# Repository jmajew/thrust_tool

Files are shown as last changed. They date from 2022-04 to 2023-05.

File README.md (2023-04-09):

# ThrustTool #

The ThrustTool is a DIY tool for measurements of an electric motor with propeller.
It allows to measure thrust, torque, rotation speed, battery voltage and current.

The project is by no means finished (especially firmware thrust++ and ThrustApp). However in current stage it works quite well allowing to obtain the results
(e.g., see auto generated report (in latex) [T-Motor F1507 with t3140 propeller](ThrustApp/data/tmotor-f1507/f1507_t3140_4s.pdf)).

### The project includes:

* [the 3d-printed tool](Doc/Tool.md)
* [custom board based on STM32 F401 mcu](Doc/Board.md)
* [firmware for the custom board](Doc/Firmware.md)
* [QT application for measurement managing and reporting](Doc/ThrustApp.md)

### 3D render of the tool
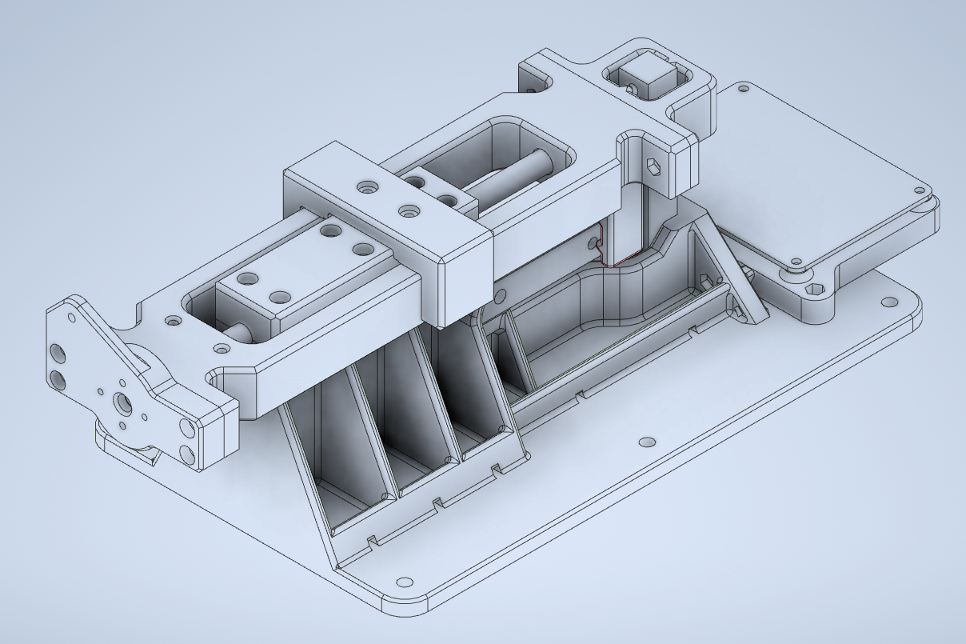
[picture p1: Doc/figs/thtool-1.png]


## Warning ##

The project is delivered as is. All responsibilities lies on the side of the user. 
Remember to take adequate security measures when testing any motor (especially powerful one).

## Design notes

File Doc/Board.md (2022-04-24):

## Custom board - thrustBoard v2

Custom measurement board (thrustBoard v2) is based on STM32 F401RETx LQFP64 MCU. 
The schematic of the thrustBoard v2 is [here](../Board/thrust_v2.pdf).

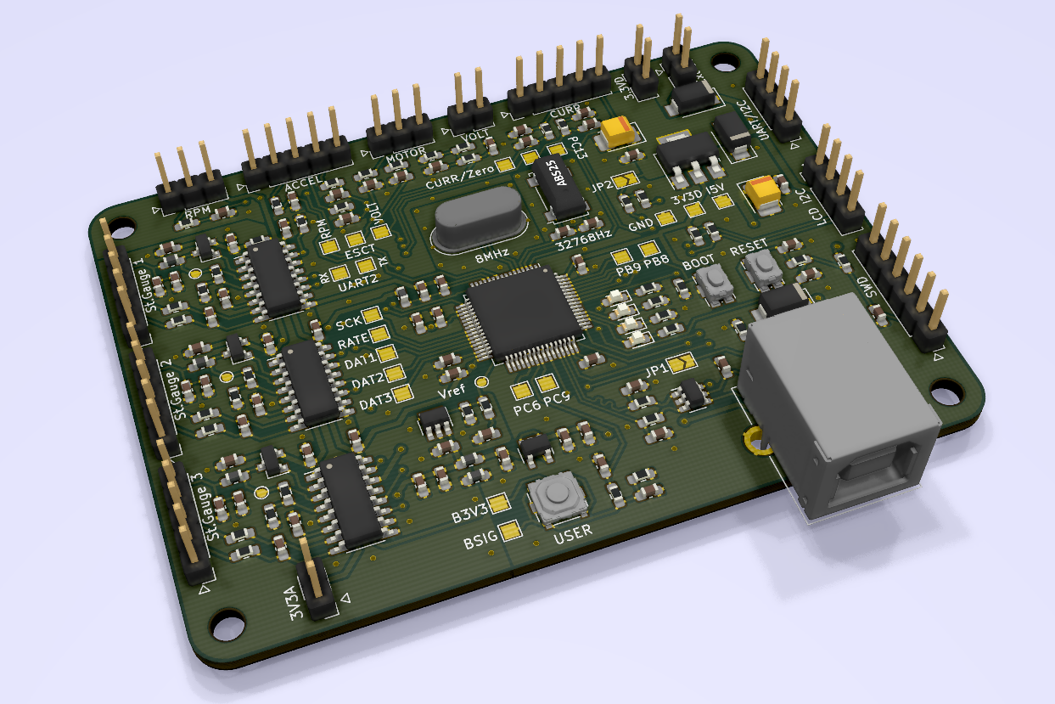
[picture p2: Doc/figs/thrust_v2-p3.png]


### Main features of the board:
* the physical board size is 84mm x 61mm.
* 3x channels of HX711 (24-Bit ADC for weight scales) - only 2 of them are actually used
* 8x 12-Bit ADC built-in inside the MCU used for battery voltage, current (2 channels), reference voltage, analog accelerometer (3 channels), MCU temperature
* SWD interface used for programming and debugging
* 1x UART or I2C communication for some future use
* 1x LCD with I2C interface to show some diagnostic data
* USB used communication with the board
* the board is powered by the USB but it is also possible use external 5V power source
* reset button, boot button (not used since programming is done by SWD), user button (currently not used in firmware)

### Recommended parts to use with the board:
* [Current sensors base on Hall sensor](https://www.pololu.com/category/118/current-sensors);
  some sensor require two channels of ADC one for current measurement and another for zero current
* ESC motor controller with telemetry (allows to obtain RPMs without additional infrared sensor), 
  e.g., [Tekko32 F3 Metal ESC (65A)](http://www.holybro.com/product/tekko32-f3-metal-esc-65a/)

### Additional notes:
- JP1 when closed allows to use USB_VBUS
- JP2 when closed enables pull-up resistor when UART/I2C is used as I2C 
- RTC crystal is not really currently needed. It was added for some possible future ideas.

### Front and back of the thrustBoard v2:
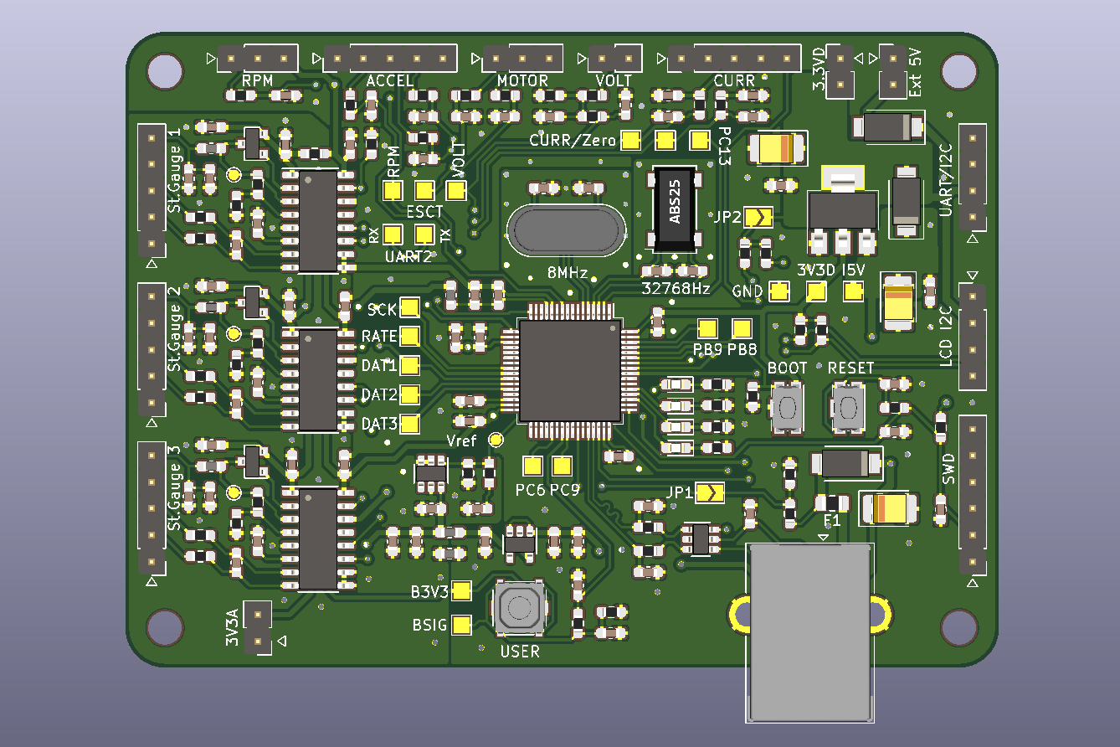
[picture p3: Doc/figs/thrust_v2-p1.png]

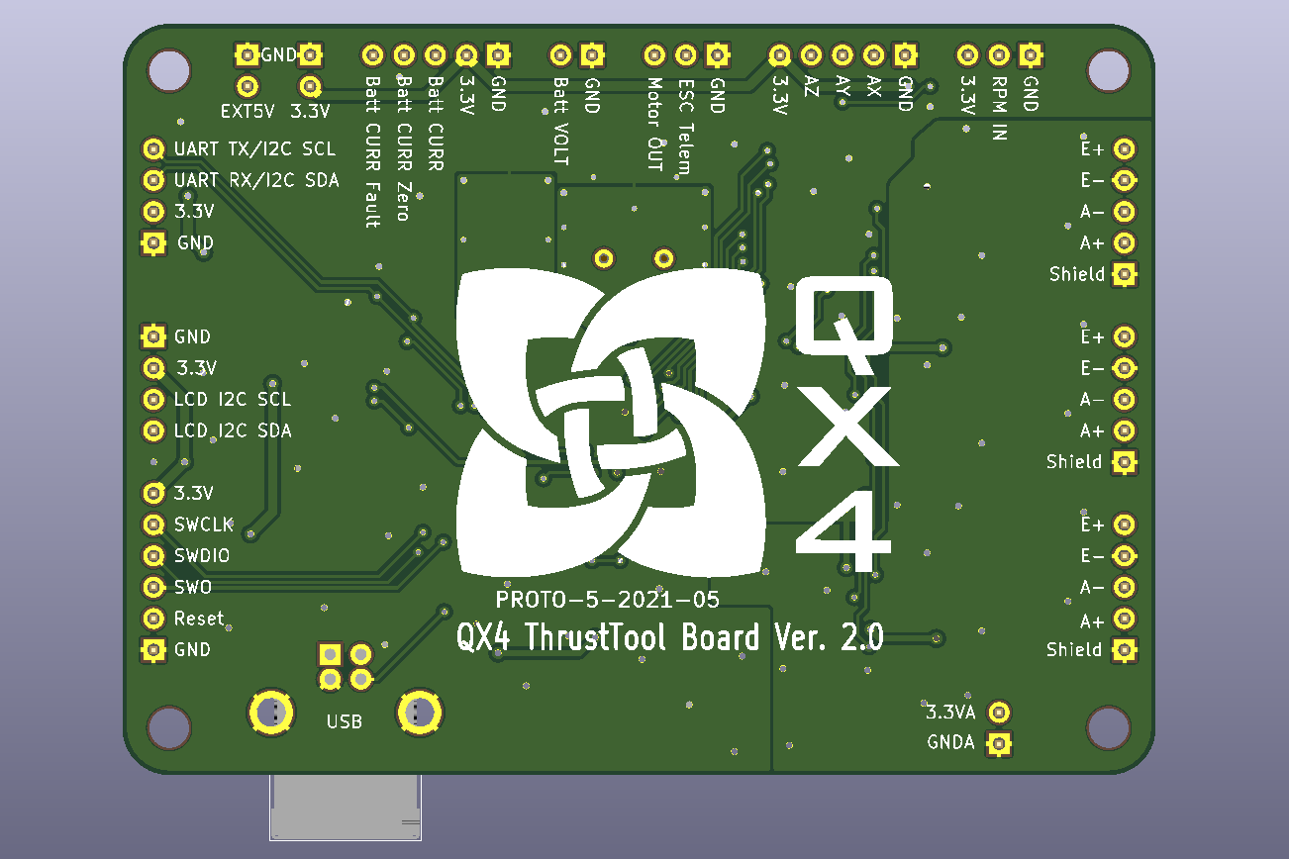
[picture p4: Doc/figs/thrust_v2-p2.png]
back


### Note

It is possible to use standard STM32 Nucleo F401RE board equipped with additional HX711 sensor boards instead of the thrustBoard v2.
Such approach require some experimenting both with hardware and firmware in order to map the pins, etc., properly.

### Picture of the board:
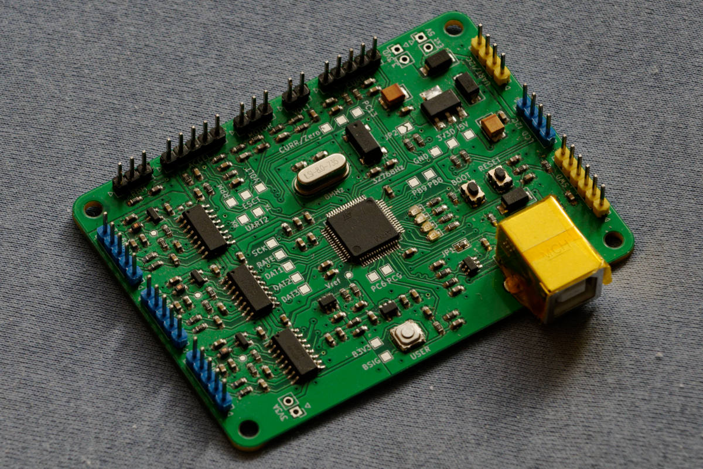
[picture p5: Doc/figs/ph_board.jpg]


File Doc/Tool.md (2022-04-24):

## Tool (3D printed)

The tool is built around two load cells: first for thrust and second for torque measurement. 
I have used load cells: 1kG for torque and 2kG for thrust - they allow measurements with resolution around 0.1G for thrust and 0.25 Gcm for torque.
The propeller should be mounted as a pusher such that flow stream behind propeller is not interacting with the tool and remain undisturbed.

### Half section of the tool:
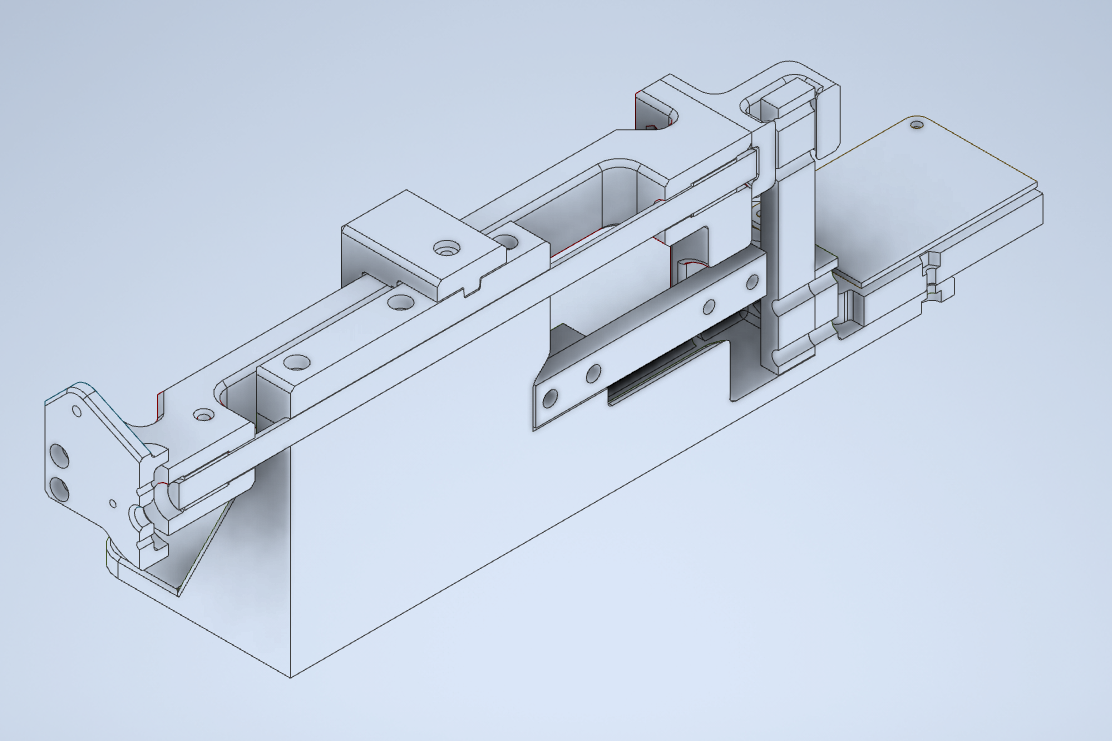
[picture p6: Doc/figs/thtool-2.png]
half section of the tool


### 3D-printed parts:
printed using PLA and without any support:
* stand
* axle mount
* spindle - use 4 perimeters
* thrust adapter
* lock - used to protect the load cells against excessive forces during, ex. transportation
* board mount
* motor mount - this part should be designed according to the motor specification, with or without infrared RPM sensor. 
  In case motor gets hot, more thermal resistant material should be used (PETG or even better ABS).

### Other elements:
* metal rod 8mm x 200mm
* [2 x plain bearing 8mm/10mm x 12mm](https://www.tme.eu/pl/en/details/wsm-0810-12/plain-bearings/igus/)
* M3 screws and nuts (length: 25mm, 16mm)

### extra 3D-printed parts:
they are not necessary but can be helpful during calibration process:
* thrust calib tray
* torque calib arm

### Picture of the working tool:
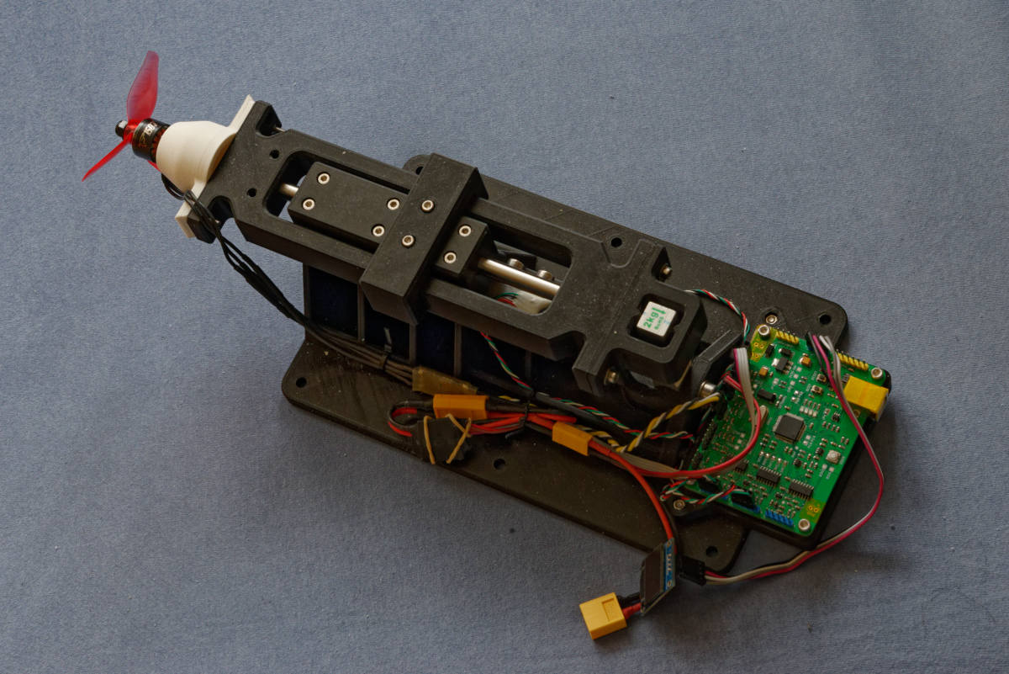
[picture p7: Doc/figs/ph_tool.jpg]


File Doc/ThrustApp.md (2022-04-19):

## ThrustApp 

ThrustApp is a QT application used for conducting measurement (tested in Win10 environment). 
It connects to the measurement board and by using serial protocol manages the process of data acquisition, receives the data
and present them in visual or tabular form. Finally it can processes the data and export a measurement report.

### Example view of the ThrustApp
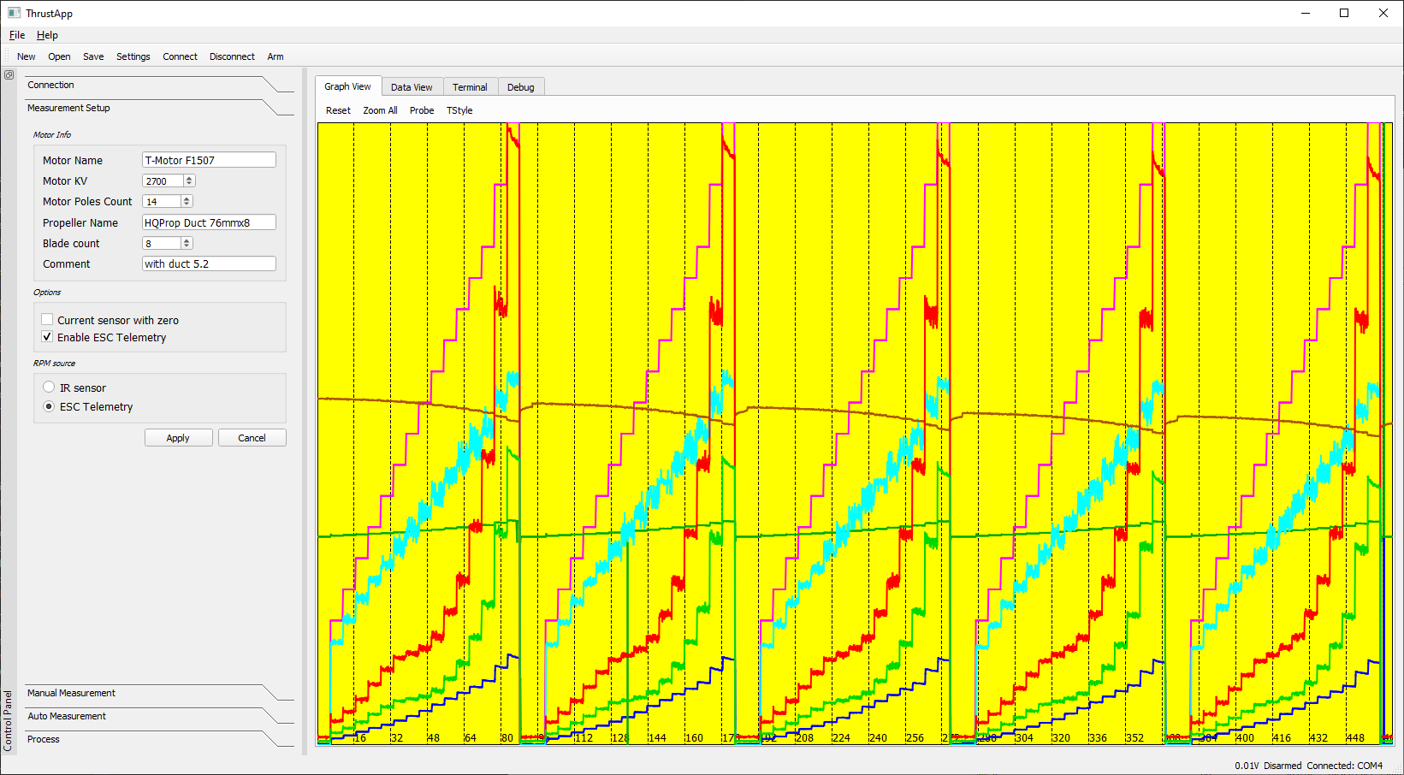
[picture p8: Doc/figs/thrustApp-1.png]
ThustApp


### Short description

The app is split in two areas: left is for controlling and right is for data presenting, terminal and protocol debugging.

#### Control widgets (for details see [Workflow](#workflow)):
* Connection
* Measurement Setup
* Manual Measurement - allows to manually start/stop data acquisition and start/stop motor with given output level (in micro-seconds)
* Auto Measurement
* Process

#### Main widgets:
* Graph View - shows data as a graph of multiple channels, both __raw__ and __cooked__. 
  It is possible to select what is shown by TStyle dialog (press *Color* to choose color, line style). 
  Ctrl+click can be used for zoom-window or Ctrl+wheel for zoom-in and zoom-out.
* Data View - shows data as a simple tabular array. Some column can be hidden for clarity
* Terminal - is used for low level connection to measurement board
* Debug - used for protocol debugging

### Workflow

* Connect to the tool via USB (the port should be visible as STMicroelectronics Virtual COM Port).
  Acceptable baud rate should be up to 500000. After successful connection info about board and firmware can be found in *Help/About* 
  and status bar should display *Connected: COMx*.
* In *Measurement Setup* put information about motor/propeller (needed only for reports) and select options. The tested options are 
  *ESC Telemetry* and *Enable ESC Telemetry*. Then press *Apply*.
* Select *Auto Measurement* and press button *Auto Create*. Choose starting and ending level and increment of motor output, 
  provide number of samples per single measurement (e.g., around 55-60 when using 10smpl/s) and 
  number of samples between measurements with motor output level 0% (preferably it should be 0). 
  After accepting the measurement table will be filled with values. You can still add or remove rows by mouse right-click menu.  
* Execute measurement setup by arming motor (main toolbar *Arm*) and pressing button *Measure Start*.
* Final step is processing data. The *Left margin* (e.g., around 10) and *Right margin* (e.g., around 4) 
  allows to select which part of single measurement is taken into account. This is necessary due to instabilities or delays with motor 
  response after changing the output level. The zero level is estimated taking into account all measurements with output level 0%.
* A report can be generated by choosing *File/Export* from menu. The report can exported as a text report
  (which contains only arrays of measurements) or as a latex file (can show also the plots). Before generating latex report, first
  the report template must be chosen (*File/Select Latex template*)

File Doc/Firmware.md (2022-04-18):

## Firmware thrust++

Firmware is written using C++ and [ChibiOS RTOS](https://www.chibios.org) (ver. ChibiOS RT 7.1.0 : HAL 8.1.0). 

The protocol implemented for communication with the window application is a derivative of the MSP protocol used if flight controller firmware 
(see, e.g., iNav or Betaflight). The terminal variables, reading and setting them is also derived from the flight controller firmware.

At the current stage of development the rpm measurements done using IR sensor needs some work. Therefore, the ESC telemetry should be  currently used as a source of the revolution speed measurement.

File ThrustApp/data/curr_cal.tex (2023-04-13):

\documentclass[10pt]{article}

\usepackage{pgfplots}
\usepackage{multirow}
\usepackage{filecontents}

\pgfplotsset{compat=1.14}

\usepackage[margin=20mm]{geometry}

\setlength{\textheight}{240 mm}

\begin{filecontents*}{table1.dat}
out,      th,    th_err, tq,     tq_err,  rpm,   rpm_err,  v,    v_err,   a,     a_err,   pin,        theff
    2e+01,       70.24,       0.323,      107.74,       2.373,        5496,        46.7,      14.736,      0.0057,       0.745,      0.0289,      10.977,       6.399
       40,      205.06,       0.344,      270.71,       2.376,        8753,        39.3,      14.471,      0.0069,       2.398,      0.0293,      34.701,       5.909
       45,      250.83,       0.585,      330.44,       2.421,        9594,        44.7,      14.340,      0.0075,       3.120,      0.0498,      44.743,       5.606
       50,      301.62,       0.747,      394.87,       2.535,       10477,        64.2,      14.193,      0.0091,       3.969,      0.0653,      56.334,       5.354
       55,      355.54,       0.714,      461.58,       2.437,       11337,        77.5,      14.018,      0.0101,       4.977,      0.0818,      69.771,       5.096
       60,      410.97,       0.735,      532.45,       2.432,       12162,        92.4,      13.821,      0.0118,       6.037,      0.0778,      83.441,       4.925
\end{filecontents*}

\begin{document}

\noindent
{\large \bf Tool info}
\vspace{3mm}

\noindent
\begin{tabular}{ll}
Serial API:  & \\ 
Board:       & \\ 
Firmware:    & \\ 
Commit:      & 
\end{tabular}
\vspace{3mm}

\noindent
{\large \bf Measurement info}
\vspace{3mm}

\noindent
\begin{tabular}{ll}
Motor:        & Generic Motor\\ 
KV:           & 0\\ 
Magnet poles: & 14\\ 
Propeler:     & \\ 
Blade count:  & 2\\ 
Note:         & 
\end{tabular}

\vspace{3mm}

%\noindent
%{\large \bf Measurement Results 1:}
%\vspace{3mm}

\subsection*{\large \bf Measurement Results 1:}

\noindent
\resizebox{\textwidth}{!}{
\begin{tabular}{|r|rr|rr|rr|rr|rr|r|r|}
\hline 
 \multirow[c]{2}{11mm}{Output [\%]} & \multicolumn{2}{l|}{Thrust [G]} & \multicolumn{2}{l|}{Torque [G cm]} & \multicolumn{2}{l|}{RPM [1/min]} 
   & \multicolumn{2}{l|}{Voltage [V]} & \multicolumn{2}{l|}{Current [A]} &\multirow{2}{14mm}{Pin [W]}  &\multirow{2}{14mm}{ThrustEff [G/W]}  \\
\cline{2-11} 
    &    mean& std dev&   mean& std dev&   mean& std dev&    mean& std dev&  mean& std dev&         &                \\
\hline
       20 &        70.24 &        0.323 &       107.74 &        2.373 &         5496 &         46.7 &       14.736 &       0.0057 &        0.745 &       0.0289 &       10.977 &        6.399 \\
       40 &       205.06 &        0.344 &       270.71 &        2.376 &         8753 &         39.3 &       14.471 &       0.0069 &        2.398 &       0.0293 &       34.701 &        5.909 \\
       45 &       250.83 &        0.585 &       330.44 &        2.421 &         9594 &         44.7 &       14.340 &       0.0075 &        3.120 &       0.0498 &       44.743 &        5.606 \\
       50 &       301.62 &        0.747 &       394.87 &        2.535 &        10477 &         64.2 &       14.193 &       0.0091 &        3.969 &       0.0653 &       56.334 &        5.354 \\
       55 &       355.54 &        0.714 &       461.58 &        2.437 &        11337 &         77.5 &       14.018 &       0.0101 &        4.977 &       0.0818 &       69.771 &        5.096 \\
       60 &       410.97 &        0.735 &       532.45 &        2.432 &        12162 &         92.4 &       13.821 &       0.0118 &        6.037 &       0.0778 &       83.441 &        4.925 \\
\hline
\end{tabular}
}

%\vspace{3mm}

\pagebreak
%\noindent
%{\large \bf Plots for Measurement Results:}
%\vspace{3mm}

\subsection*{Plots for Measurement Results:}
%\noindent
\centerline{
\hspace{-10mm}
\begin{tikzpicture}
	\begin{axis}[
		height=8cm,
		width=8cm,  %\textwidth,
		xmin=15,
		xmax=105,
		ymin=0,
		minor x tick num=3,
		minor y tick num=3,
		ticklabel style = {font=\tiny},
		grid=both,
		major grid style={gray!80},
		minor grid style={gray!25},
		xlabel={\footnotesize Motor Output [\%]},
		ylabel={\footnotesize Thrust [G]},
		%ylabel style={ yshift = {-1mm}, },
		legend pos=north west,
		legend style={draw=none}]
	\addplot[
		blue, mark options={black, scale=0.175},
		smooth, 
		error bars/.cd, 
		y fixed,
		y dir=both, 
		y explicit,
	] 
	table [x=out, y=th, y error=th_err, col sep=comma] {table1.dat};

	\end{axis}
\end{tikzpicture}
\hspace{5mm}
\begin{tikzpicture}
	\begin{axis}[
		height=8cm,
		width=8cm,  %\textwidth,
		xmin=15,
		xmax=105,
		ymin=0,
		minor x tick num=3,
		minor y tick num=3,
		ticklabel style = {font=\tiny},
		grid=both,
		major grid style={gray!80},
		minor grid style={gray!25},
		xlabel={\footnotesize Motor Output [\%]},
		ylabel={\footnotesize Torque [G cm]},
		legend pos=north west,
		legend style={draw=none}]
	\addplot[
		blue, mark options={black, scale=0.175},
		smooth, 
		error bars/.cd, 
		y fixed,
		y dir=both, 
		y explicit,
	] 
	table [x=out, y=tq, y error=tq_err, col sep=comma] {table1.dat};

	\end{axis}
\end{tikzpicture}
}
  
%\noindent 
\centerline{
\vspace{3mm}
\begin{tikzpicture}
	\begin{axis}[
		height=8cm,
		width=8cm,  %\textwidth,
		xmin=15,
		xmax=105,
		%ymin=0,
		minor x tick num=3,
		minor y tick num=3,	
		ticklabel style = {font=\tiny},
		tick scale binop=\times, %base 10:-3,
		grid=both,
		major grid style={gray!80},
		minor grid style={gray!25},
		xlabel={\footnotesize Motor Output [\%]},
		ylabel={\footnotesize RPM [1/min]},
		legend pos=north west,
		legend style={draw=none}]
	\addplot[
		blue, mark options={black, scale=0.175},
		smooth, 
		error bars/.cd, 
			y fixed,
			y dir=both, 
			y explicit,
	] 
	table [x=out, y=rpm, y error=rpm_err, col sep=comma] {table1.dat};

	\end{axis}
\end{tikzpicture}
\hspace{4.65mm}
\begin{tikzpicture}
	\begin{axis}[
		height=8cm,
		width=8cm,
		axis y line*=right,		
		xmin=15,
		xmax=105,
		ymin=0,
		minor x tick num=3,
		ticklabel style = {font=\tiny},
		grid=both,
		xlabel={\footnotesize Motor Output [\%]},
		ylabel={\footnotesize Current [A]},
		legend pos=north west,
		legend style={draw=none}]
	\addplot[
	  blue, mark options={black, scale=0.175},
	  smooth, 
	  error bars/.cd, 
		y fixed,
		y dir=both, 
		y explicit
	] 
	table [x=out, y=a, y error=a_err, col sep=comma] {table1.dat};

	\end{axis}
	\begin{axis}[
		height=8cm,
		width=8cm,  %\textwidth,
		axis y line*=left,
		axis x line=none,
		scaled y ticks=false,
		ticklabel style = {font=\tiny},
		grid style=dashed,
		grid=major,
		ylabel={\footnotesize Voltage [V]},
		legend style={
			nodes={scale=0.5, transform shape},
			cells={anchor=east},
			% legend pos=south east,
			at={(0.5,0.97)},anchor=north,
		}
	]
%	\addlegendimage{/pgfplots/refstyle=plot_1}\addlegendentry{Current [A]}
	\addplot[
		red, mark options={red, scale=0.15},
		smooth,
		error bars/.cd, 
		y fixed,
		y dir=both, 
		y explicit  
	] 
	table [x=out, y=v, y error=v_err, col sep=comma] {table1.dat};

%	\addlegendentry{Voltage [V]}
	\end{axis}
\end{tikzpicture}
\vspace{3mm}
}

%\noindent 
\centerline{
\hspace{-10mm}
\begin{tikzpicture}
	\begin{axis}[
		height=8cm,
		width=8cm,  %\textwidth,
		xmin=15,
		xmax=105,
		ymin=0,
		minor x tick num=3,
		minor y tick num=3,		
		ticklabel style = {font=\tiny},
		grid=both,
		major grid style={gray!80},
		minor grid style={gray!25},
		xlabel={\footnotesize Motor Output [\%]},
		ylabel={\footnotesize Power In [W]},
		legend pos=north west,
		legend style={
			nodes={scale=0.75, transform shape},
			cells={anchor=west},
			legend pos=north west,
		}	
	]			
	\addplot[
		blue, mark=*, mark options={blue, scale=0.5},
		smooth, 
	] 
	table [x=out, y=pin, col sep=comma] {table1.dat};

	\end{axis}
\end{tikzpicture}
\hspace{9mm}
\begin{tikzpicture}
	\begin{axis}[
		height=8cm,
		width=8cm,  %\textwidth,
		xmin=15,
		xmax=105,
		minor x tick num=3,
		minor y tick num=3,
		ticklabel style = {font=\tiny},
		grid=both,
		major grid style={gray!80},
		minor grid style={gray!25},
		xlabel={\footnotesize Motor Output [\%]},
		ylabel={\footnotesize Thrust Efficiency [G/W]},
		legend pos=north west,
		legend style={draw=none}]
	\addplot[
		blue, mark=*, mark options={blue, scale=0.5},
		smooth, 
	] 
	table [x=out, y=theff, col sep=comma] {table1.dat};

	\end{axis}
\end{tikzpicture}
}
	
\end{document}

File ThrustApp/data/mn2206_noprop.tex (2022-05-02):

\documentclass[10pt]{article}

\usepackage{pgfplots}
\usepackage{multirow}
\usepackage{filecontents}

\pgfplotsset{compat=1.14}

\usepackage[margin=20mm]{geometry}

\setlength{\textheight}{240 mm}

\begin{filecontents*}{table1.dat}
out,      th,    th_err, tq,     tq_err,  rpm,   rpm_err,  v,    v_err,   a,     a_err,   pin,        theff
    2e+01,        0.75,       4.004,        4.67,       3.013,        4759,        10.9,      12.141,      0.0039,       0.130,      0.0088,       1.580,       0.474
       25,        0.65,       4.004,        4.80,       3.013,        5899,        17.7,      12.140,      0.0041,       0.166,      0.0126,       2.014,       0.323
       30,       -0.30,       4.005,        4.98,       3.013,        7108,        27.4,      12.141,      0.0049,       0.188,      0.0129,       2.287,      -0.129
       35,       -0.30,       4.004,        5.04,       3.013,        8272,        32.6,      12.135,      0.0042,       0.242,      0.0171,       2.942,      -0.104
       40,       -0.38,       4.004,        5.62,       3.013,        9472,        56.0,      12.133,      0.0031,       0.263,      0.0177,       3.194,      -0.119
       45,       -1.53,       4.004,        4.44,       3.014,       10621,        81.1,      12.134,      0.0052,       0.294,      0.0325,       3.573,      -0.430
       50,       -2.90,       4.004,        4.27,       3.013,       11750,        85.6,      12.129,      0.0038,       0.322,      0.0218,       3.900,      -0.744
       55,       -3.37,       4.004,        3.33,       3.014,       12883,        89.5,      12.127,      0.0044,       0.373,      0.0309,       4.520,      -0.746
       60,       -3.35,       4.004,        2.68,       3.015,       14102,        69.3,      12.123,      0.0040,       0.403,      0.0262,       4.890,      -0.684
       65,       -3.38,       4.004,        1.43,       3.044,       15312,        95.8,      12.123,      0.0040,       0.429,      0.0445,       5.203,      -0.650
       70,       -3.38,       4.004,        0.38,       3.015,       16479,       119.5,      12.121,      0.0039,       0.455,      0.0333,       5.512,      -0.614
       75,       -3.38,       4.004,        0.92,       3.018,       17717,        80.4,      12.119,      0.0047,       0.470,      0.0248,       5.698,      -0.593
       80,       -7.57,       4.043,        5.10,       3.017,       18809,       122.2,      12.116,      0.0043,       0.488,      0.0333,       5.915,      -1.280
       90,       -4.35,       4.005,        6.84,       3.013,       21142,        92.4,      12.113,      0.0035,       0.535,      0.0127,       6.485,      -0.671
      100,       -0.64,       4.009,        4.66,       3.014,       23243,       100.8,      12.109,      0.0048,       0.592,      0.0144,       7.167,      -0.089
\end{filecontents*}

\begin{document}

\noindent
{\large \bf Tool info}
\vspace{3mm}

\noindent
\begin{tabular}{ll}
Serial API:  & 1:1.0\\ 
Board:       & Custom STM32F401RE thrustBoard v2\\ 
Firmware:    & thrust++ : ChibiOS RT 7.1.0 : HAL 8.1.0\\ 
Commit:      & [7ea798b] : Apr 25 2022 - 18:19:20
\end{tabular}
\vspace{3mm}

\noindent
{\large \bf Measurement info}
\vspace{3mm}

\noindent
\begin{tabular}{ll}
Motor:        & T-Motor MN2206-13\\ 
KV:           & 2000\\ 
Magnet poles: & 14\\ 
Propeler:     & no propeller\\ 
Blade count:  & 0\\ 
Note:         & 
\end{tabular}

\vspace{3mm}

\noindent
{\large \bf Measurement Results 1:}
\vspace{3mm}

\noindent
\resizebox{\textwidth}{!}{
\begin{tabular}{|r|rr|rr|rr|rr|rr|r|r|}
\hline 
 \multirow[c]{2}{11mm}{Output [\%]} & \multicolumn{2}{l|}{Thrust [G]} & \multicolumn{2}{l|}{Torque [G cm]} & \multicolumn{2}{l|}{RPM [1/min]} 
   & \multicolumn{2}{l|}{Voltage [V]} & \multicolumn{2}{l|}{Current [A]} &\multirow{2}{14mm}{Pin [W]}  &\multirow{2}{14mm}{ThrustEff [G/W]}  \\
\cline{2-11} 
    &    mean& std dev&   mean& std dev&   mean& std dev&    mean& std dev&  mean& std dev&         &                \\
\hline
       20 &         0.75 &        4.004 &         4.67 &        3.013 &         4759 &         10.9 &       12.141 &       0.0039 &        0.130 &       0.0088 &        1.580 &        0.474 \\
       25 &         0.65 &        4.004 &         4.80 &        3.013 &         5899 &         17.7 &       12.140 &       0.0041 &        0.166 &       0.0126 &        2.014 &        0.323 \\
       30 &        -0.30 &        4.005 &         4.98 &        3.013 &         7108 &         27.4 &       12.141 &       0.0049 &        0.188 &       0.0129 &        2.287 &       -0.129 \\
       35 &        -0.30 &        4.004 &         5.04 &        3.013 &         8272 &         32.6 &       12.135 &       0.0042 &        0.242 &       0.0171 &        2.942 &       -0.104 \\
       40 &        -0.38 &        4.004 &         5.62 &        3.013 &         9472 &         56.0 &       12.133 &       0.0031 &        0.263 &       0.0177 &        3.194 &       -0.119 \\
       45 &        -1.53 &        4.004 &         4.44 &        3.014 &        10621 &         81.1 &       12.134 &       0.0052 &        0.294 &       0.0325 &        3.573 &       -0.430 \\
       50 &        -2.90 &        4.004 &         4.27 &        3.013 &        11750 &         85.6 &       12.129 &       0.0038 &        0.322 &       0.0218 &        3.900 &       -0.744 \\
       55 &        -3.37 &        4.004 &         3.33 &        3.014 &        12883 &         89.5 &       12.127 &       0.0044 &        0.373 &       0.0309 &        4.520 &       -0.746 \\
       60 &        -3.35 &        4.004 &         2.68 &        3.015 &        14102 &         69.3 &       12.123 &       0.0040 &        0.403 &       0.0262 &        4.890 &       -0.684 \\
       65 &        -3.38 &        4.004 &         1.43 &        3.044 &        15312 &         95.8 &       12.123 &       0.0040 &        0.429 &       0.0445 &        5.203 &       -0.650 \\
       70 &        -3.38 &        4.004 &         0.38 &        3.015 &        16479 &        119.5 &       12.121 &       0.0039 &        0.455 &       0.0333 &        5.512 &       -0.614 \\
       75 &        -3.38 &        4.004 &         0.92 &        3.018 &        17717 &         80.4 &       12.119 &       0.0047 &        0.470 &       0.0248 &        5.698 &       -0.593 \\
       80 &        -7.57 &        4.043 &         5.10 &        3.017 &        18809 &        122.2 &       12.116 &       0.0043 &        0.488 &       0.0333 &        5.915 &       -1.280 \\
       90 &        -4.35 &        4.005 &         6.84 &        3.013 &        21142 &         92.4 &       12.113 &       0.0035 &        0.535 &       0.0127 &        6.485 &       -0.671 \\
      100 &        -0.64 &        4.009 &         4.66 &        3.014 &        23243 &        100.8 &       12.109 &       0.0048 &        0.592 &       0.0144 &        7.167 &       -0.089 \\
\hline
\end{tabular}
}

\vspace{3mm}

\pagebreak
\noindent
{\large \bf Plots for Measurement Results:}
\vspace{5mm}

\noindent
\begin{tikzpicture}
	\begin{axis}[
		height=8cm,
		width=8cm,  %\textwidth,
		ticklabel style = {font=\tiny},
		minor tick num=4,
		ymin=0,
		grid=both,
		major grid style={gray!80},
		minor grid style={gray!25},
		xlabel={\footnotesize Motor Output [\%]},
		ylabel={\footnotesize Thrust [G]},
		legend pos=north west,
		legend style={draw=none}]
	\addplot[
		blue, mark options={black, scale=0.175},
		smooth, 
		error bars/.cd, 
		y fixed,
		y dir=both, 
		y explicit,
	] 
	table [x=out, y=th, y error=th_err, col sep=comma] {table1.dat};

	\end{axis}
\end{tikzpicture}
\hspace{3mm}
\begin{tikzpicture}
	\begin{axis}[
		height=8cm,
		width=8cm,  %\textwidth,
		ticklabel style = {font=\tiny},
		minor tick num=4,
		ymin=0,
		grid=both,
		major grid style={gray!80},
		minor grid style={gray!25},
		xlabel={\footnotesize Motor Output [\%]},
		ylabel={\footnotesize Torque [G cm]},
		legend pos=north west,
		legend style={draw=none}]
	\addplot[
		blue, mark options={black, scale=0.175},
		smooth, 
		error bars/.cd, 
		y fixed,
		y dir=both, 
		y explicit,
	] 
	table [x=out, y=tq, y error=tq_err, col sep=comma] {table1.dat};

	\end{axis}
\end{tikzpicture}
  
\noindent 
\vspace{3mm}
\begin{tikzpicture}
	\begin{axis}[
		height=8cm,
		width=8cm,  %\textwidth,
		ticklabel style = {font=\tiny},
		tick scale binop=\times, %base 10:-3,
		minor tick num=4,
		grid=both,
		major grid style={gray!80},
		minor grid style={gray!25},
		xlabel={\footnotesize Motor Output [\%]},
		ylabel={\footnotesize RPM [1/min]},
		legend pos=north west,
		legend style={draw=none}]
	\addplot[
		blue, mark options={black, scale=0.175},
		smooth, 
		error bars/.cd, 
			y fixed,
			y dir=both, 
			y explicit,
	] 
	table [x=out, y=rpm, y error=rpm_err, col sep=comma] {table1.dat};

	\end{axis}
\end{tikzpicture}
\hspace{4.65mm}
\begin{tikzpicture}
	\begin{axis}[
		height=8cm,
		width=8cm,
		ticklabel style = {font=\tiny},
		ymin=0,
		grid=both,
		xlabel={\footnotesize Motor Output [\%]},
		ylabel={\footnotesize Current [A]},
		legend pos=north west,
		legend style={draw=none}]
	\addplot[
	  blue, mark options={black, scale=0.175},
	  smooth, 
	  error bars/.cd, 
		y fixed,
		y dir=both, 
		y explicit
	] 
	table [x=out, y=a, y error=a_err, col sep=comma] {table1.dat};

	\end{axis}
	\begin{axis}[
		height=8cm,
		width=8cm,  %\textwidth,
		axis y line*=right,
		axis x line=none,
		scaled y ticks=false,
		ticklabel style = {font=\tiny},
		grid style=dashed,
		grid=major,
		ylabel={\footnotesize Voltage [V]},
		legend style={
			nodes={scale=0.5, transform shape},
			cells={anchor=east},
			% legend pos=south east,
			at={(0.5,0.97)},anchor=north,
		}
	]
%	\addlegendimage{/pgfplots/refstyle=plot_1}\addlegendentry{Current [A]}
	\addplot[
		red, mark options={red, scale=0.15},
		smooth,
		error bars/.cd, 
		y fixed,
		y dir=both, 
		y explicit  
	] 
	table [x=out, y=v, y error=v_err, col sep=comma] {table1.dat};

%	\addlegendentry{Voltage [V]}
	\end{axis}
\end{tikzpicture}
\vspace{3mm}

\noindent 
\begin{tikzpicture}
	\begin{axis}[
		height=8cm,
		width=8cm,  %\textwidth,
		ticklabel style = {font=\tiny},
		minor tick num=4,
		ymin=0,
		grid=both,
		major grid style={gray!80},
		minor grid style={gray!25},
		xlabel={\footnotesize Motor Output [\%]},
		ylabel={\footnotesize Power In [W]},
		legend pos=north west,
		legend style={
			nodes={scale=0.75, transform shape},
			cells={anchor=west},
			legend pos=north west,
		}	
	]			
	\addplot[
		blue, mark=*, mark options={blue, scale=0.5},
		smooth, 
	] 
	table [x=out, y=pin, col sep=comma] {table1.dat};

	\end{axis}
	\end{tikzpicture}
\hspace{3mm}
	\begin{tikzpicture}
	\begin{axis}[
		height=8cm,
		width=8cm,  %\textwidth,
		ticklabel style = {font=\tiny},
		minor tick num=4,
		grid=both,
		major grid style={gray!80},
		minor grid style={gray!25},
		xlabel={\footnotesize Motor Output [\%]},
		ylabel={\footnotesize Thrust Efficiency [G/W]},
		legend pos=north west,
		legend style={draw=none}]
	\addplot[
		blue, mark=*, mark options={blue, scale=0.5},
		smooth, 
	] 
	table [x=out, y=theff, col sep=comma] {table1.dat};

	\end{axis}
\end{tikzpicture}

\end{document}

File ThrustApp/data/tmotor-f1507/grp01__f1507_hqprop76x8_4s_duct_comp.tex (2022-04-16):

\documentclass[10pt]{article}

\usepackage{pgfplots}
\usepackage{multirow}
\usepackage{filecontents}

\pgfplotsset{compat=1.14}

\usepackage[margin=20mm]{geometry}

\setlength{\textheight}{240 mm}

% \begin{filecontents*}{table1.dat}
% out,      th,    th_err, tq,     tq_err,  rpm,   rpm_err,  v,    v_err,   a,     a_err,   pin,        theff,
    % 2e+01,       28.52,       0.352,       48.79,       1.484,        7792,        69.8,      16.667,      0.0058,       0.479,      0.0181,       7.976,       3.575,
       % 25,       45.73,       0.413,       75.40,       1.658,        9613,       106.7,      16.651,      0.0086,       0.752,      0.0213,      12.515,       3.654,
       % 30,       67.16,       0.353,      107.87,       1.504,       11336,       114.7,      16.624,      0.0085,       1.097,      0.0282,      18.233,       3.683,
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
       60,      211.97,       1.136,      325.09,       1.014,       19533,       583.1,      16.358,      0.0109,       2.317,      0.0438,      37.908,       5.592
       65,      243.71,       0.752,      369.21,       1.334,       20708,       426.4,      16.284,      0.0133,       2.926,      0.0548,      47.641,       5.115
       70,      278.24,       0.840,      411.30,       1.363,       22175,       511.6,      16.196,      0.0127,       3.798,      0.0963,      61.514,       4.523
       75,      309.61,       2.277,      463.93,       3.978,       23169,       449.1,      16.097,      0.0126,       5.096,      0.0732,      82.030,       3.774
       80,      339.82,       3.009,      514.46,       4.794,       24354,       545.8,      15.990,      0.0097,       6.883,      0.0699,     110.062,       3.088
       90,      410.71,       2.651,      602.54,       5.925,       26446,       456.2,      15.806,      0.0173,      11.040,      0.1127,     174.498,       2.354
      100,      460.15,       3.974,      689.96,       7.139,       27885,       318.5,      15.596,      0.0183,      15.245,      0.1090,     237.763,       1.935
\end{filecontents*}

\begin{filecontents*}{table2.dat}
out,      th,    th_err, tq,     tq_err,  rpm,   rpm_err,  v,    v_err,   a,     a_err,   pin,        theff,
    2e+01,       36.19,       0.901,       43.11,       0.289,        8233,        87.6,      16.675,      0.0065,       0.391,      0.0140,       6.524,       5.547
       25,       54.59,       0.774,       68.57,       0.268,       10014,       116.3,      16.657,      0.0091,       0.622,      0.0186,      10.360,       5.269
       30,       78.09,       0.777,       91.36,       0.381,       11772,       157.1,      16.632,      0.0084,       0.932,      0.0206,      15.494,       5.040
       35,      101.89,       0.824,      121.68,       0.569,       13238,       188.5,      16.608,      0.0076,       1.298,      0.0205,      21.550,       4.728
       40,      121.84,       0.830,      145.77,       0.749,       14480,       169.5,      16.576,      0.0078,       1.651,      0.0263,      27.369,       4.452
       45,      148.23,       0.844,      174.95,       0.907,       15979,       523.5,      16.541,      0.0093,       1.943,      0.0254,      32.141,       4.612
       50,      177.38,       0.891,      214.64,       0.795,       17415,       300.2,      16.494,      0.0112,       2.052,      0.0259,      33.843,       5.241
       55,      209.49,       0.896,      254.91,       1.193,       18673,       435.7,      16.435,      0.0111,       2.183,      0.0356,      35.875,       5.839
       60,      248.30,       1.149,      287.80,       1.215,       20116,       556.9,      16.372,      0.0092,       2.478,      0.0411,      40.566,       6.121
       65,      286.57,       1.603,      338.44,       2.536,       21542,       518.3,      16.297,      0.0157,       3.087,      0.0412,      50.310,       5.696
       70,      323.12,       1.204,      380.84,       2.177,       22909,       526.4,      16.216,      0.0113,       3.863,      0.0609,      62.637,       5.159
       75,      360.33,       1.595,      432.03,       1.998,       24258,       720.2,      16.121,      0.0118,       5.183,      0.0600,      83.550,       4.313
       80,      398.91,       1.761,      471.44,       2.419,       25330,       403.9,      16.013,      0.0137,       6.872,      0.0843,     110.043,       3.625
       90,      485.15,       3.696,      571.83,       6.384,       27755,       416.2,      15.827,      0.0174,      10.574,      0.1176,     167.343,       2.899
      100,      551.97,       6.166,      651.32,      10.546,       29308,       283.0,      15.616,      0.0170,      14.701,      0.1102,     229.564,       2.404
\end{filecontents*}

\begin{document}

\noindent
{\large \bf Tool info}
\vspace{3mm}

\noindent
\begin{tabular}{ll}
Serial API : 	&1:1.0  \\
Board	:		&Custom STM32F401RE thrustBoard v2  \\
Firmware :		&thrust++ : ChibiOS RT 7.1.0 : HAL 8.1.0  \\
Commit :		&[28e06d2] : Mar 20 2022 - 17:31:34
\end{tabular}
\vspace{3mm}

\noindent
{\large \bf Measurement info}
\vspace{3mm}

\noindent
\begin{tabular}{ll}
Motor : 		&T-Motor F1507  \\
KV : 			&2700  \\
Magnet poles : 	&14  \\

Propeler : 		&HQProp Duct 76mmx8 \\
Blade number : 	&8  \\
Note :			&comparison of the performance with and without the duct
\end{tabular}

\vspace{3mm}

\noindent
{\large \bf Measurement Results without Duct:}
\vspace{3mm}

% \noindent
% \resizebox{\textwidth}{!}{
% \begin{tabular}{|r|rr|rr|rr|rr|rr|r|r|}
% \hline 
 % \multirow[c]{2}{11mm}{Output [\%]} & \multicolumn{2}{l|}{Thrust [G]} & \multicolumn{2}{l|}{Torque [G cm]} & \multicolumn{2}{l|}{RPM [1/min]} 
   % & \multicolumn{2}{l|}{Voltage [V]} & \multicolumn{2}{l|}{Current [A]} &\multirow{2}{14mm}{Pin [W]}  &\multirow{2}{14mm}{ThrustEff [G/W]}  \\
% \cline{2-11} 
    % &    mean& std dev&   mean& std dev&   mean& std dev&    mean& std dev&  mean& std dev&         &                \\
% \hline
       % 20 &        28.52 &        0.352 &        48.79 &        1.484 &         7792 &         69.8 &       16.667 &       0.0058 &        0.479 &       0.0181 &        7.976 &        3.575 \\
       % 25 &        45.73 &        0.413 &        75.40 &        1.658 &         9613 &        106.7 &       16.651 &       0.0086 &        0.752 &       0.0213 &       12.515 &        3.654 \\
       % 30 &        67.16 &        0.353 &       107.87 &        1.504 &        11336 &        114.7 &       16.624 &       0.0085 &        1.097 &       0.0282 &       18.233 &        3.683 \\
       % 35 &        89.74 &        0.622 &       145.08 &        1.508 &        13035 &        244.1 &       16.590 &       0.0072 &        1.349 &       0.0319 &       22.377 &        4.010 \\
       % 40 &       116.48 &        0.525 &       184.78 &        1.530 &        14636 &        359.5 &       16.545 &       0.0079 &        1.732 &       0.0391 &       28.650 &        4.066 \\
       % 45 &       140.28 &        0.459 &       223.05 &        1.544 &        16144 &        432.4 &       16.498 &       0.0092 &        2.276 &       0.0577 &       37.552 &        3.736 \\
       % 50 &       159.23 &        0.803 &       263.47 &        1.655 &        17443 &        254.6 &       16.440 &       0.0088 &        2.895 &       0.0497 &       47.590 &        3.346 \\
       % 55 &       199.86 &        0.717 &       306.46 &        1.758 &        18786 &        642.6 &       16.378 &       0.0086 &        3.828 &       0.0309 &       62.691 &        3.188 \\
       % 60 &       225.03 &        0.488 &       347.42 &        1.872 &        19902 &        409.7 &       16.314 &       0.0117 &        4.784 &       0.0448 &       78.042 &        2.883 \\
       % 65 &       261.16 &        1.146 &       389.64 &        2.552 &        20940 &        490.7 &       16.243 &       0.0103 &        5.820 &       0.0559 &       94.541 &        2.762 \\
       % 70 &       288.82 &        0.846 &       424.86 &        2.126 &        22056 &        467.9 &       16.159 &       0.0125 &        6.790 &       0.0551 &      109.720 &        2.632 \\
       % 75 &       315.84 &        1.026 &       473.27 &        2.894 &        23069 &        813.1 &       16.064 &       0.0099 &        7.525 &       0.0396 &      120.886 &        2.613 \\
       % 80 &       339.84 &        0.699 &       512.42 &        2.396 &        24065 &        974.1 &       15.968 &       0.0133 &        8.138 &       0.0612 &      129.947 &        2.615 \\
       % 85 &       370.79 &        2.068 &       544.51 &        4.284 &        25095 &        346.5 &       15.862 &       0.0127 &        9.382 &       0.1184 &      148.818 &        2.492 \\
       % 90 &       400.86 &        1.511 &       583.28 &        3.054 &        25929 &        513.5 &       15.755 &       0.0146 &       11.318 &       0.0954 &      178.317 &        2.248 \\
       % 95 &       424.20 &        2.412 &       622.93 &        5.510 &        26641 &        399.7 &       15.637 &       0.0140 &       13.168 &       0.0827 &      205.906 &        2.060 \\
      % 100 &       442.41 &        3.998 &       661.31 &        5.523 &        27154 &        224.3 &       15.523 &       0.0112 &       14.947 &       0.0646 &      232.017 &        1.907 \\
% \hline
% \end{tabular}
% }
\noindent
\resizebox{\textwidth}{!}{
\begin{tabular}{|r|rr|rr|rr|rr|rr|r|r|}
\hline 
 \multirow[c]{2}{11mm}{Output [\%]} & \multicolumn{2}{l|}{Thrust [G]} & \multicolumn{2}{l|}{Torque [G cm]} & \multicolumn{2}{l|}{RPM [1/min]} 
   & \multicolumn{2}{l|}{Voltage [V]} & \multicolumn{2}{l|}{Current [A]} &\multirow{2}{14mm}{Pin [W]}  &\multirow{2}{14mm}{ThrustEff [G/W]}  \\
\cline{2-11} 
    &    mean& std dev&   mean& std dev&   mean& std dev&    mean& std dev&  mean& std dev&         &                \\
\hline
       20 &        30.04 &        0.208 &        49.06 &        0.202 &         8138 &        121.4 &       16.668 &       0.0072 &        0.408 &       0.0121 &        6.800 &        4.417 \\
       25 &        47.24 &        0.273 &        73.99 &        0.350 &         9842 &         80.8 &       16.649 &       0.0073 &        0.664 &       0.0181 &       11.058 &        4.273 \\
       30 &        66.96 &        0.173 &       103.19 &        0.222 &        11444 &        115.9 &       16.627 &       0.0081 &        0.988 &       0.0145 &       16.424 &        4.077 \\
       35 &        85.92 &        0.248 &       131.30 &        0.202 &        12763 &        243.4 &       16.601 &       0.0075 &        1.346 &       0.0201 &       22.352 &        3.844 \\
       40 &       106.30 &        0.386 &       163.26 &        0.409 &        14104 &        252.7 &       16.567 &       0.0074 &        1.766 &       0.0253 &       29.257 &        3.633 \\
       45 &       125.50 &        0.404 &       195.91 &        0.415 &        15512 &        376.6 &       16.529 &       0.0099 &        1.924 &       0.0267 &       31.798 &        3.947 \\
       50 &       144.74 &        2.850 &       234.91 &        1.405 &        16786 &        404.6 &       16.480 &       0.0082 &        1.971 &       0.0373 &       32.486 &        4.456 \\
       55 &       181.63 &        0.499 &       275.72 &        0.804 &        18267 &        291.4 &       16.427 &       0.0127 &        2.083 &       0.0535 &       34.224 &        5.307 \\
       60 &       211.97 &        1.136 &       325.09 &        1.014 &        19533 &        583.1 &       16.358 &       0.0109 &        2.317 &       0.0438 &       37.908 &        5.592 \\
       65 &       243.71 &        0.752 &       369.21 &        1.334 &        20708 &        426.4 &       16.284 &       0.0133 &        2.926 &       0.0548 &       47.641 &        5.115 \\
       70 &       278.24 &        0.840 &       411.30 &        1.363 &        22175 &        511.6 &       16.196 &       0.0127 &        3.798 &       0.0963 &       61.514 &        4.523 \\
       75 &       309.61 &        2.277 &       463.93 &        3.978 &        23169 &        449.1 &       16.097 &       0.0126 &        5.096 &       0.0732 &       82.030 &        3.774 \\
       80 &       339.82 &        3.009 &       514.46 &        4.794 &        24354 &        545.8 &       15.990 &       0.0097 &        6.883 &       0.0699 &      110.062 &        3.088 \\
       90 &       410.71 &        2.651 &       602.54 &        5.925 &        26446 &        456.2 &       15.806 &       0.0173 &       11.040 &       0.1127 &      174.498 &        2.354 \\
      100 &       460.15 &        3.974 &       689.96 &        7.139 &        27885 &        318.5 &       15.596 &       0.0183 &       15.245 &       0.1090 &      237.763 &        1.935 \\
\hline
\end{tabular}
}

\vspace{3mm}

\noindent
{\large \bf Measurement Results with Duct:}
\vspace{3mm}

\noindent
\resizebox{\textwidth}{!}{
\begin{tabular}{|r|rr|rr|rr|rr|rr|r|r|}
\hline 
 \multirow[c]{2}{11mm}{Output [\%]} & \multicolumn{2}{l|}{Thrust [G]} & \multicolumn{2}{l|}{Torque [G cm]} & \multicolumn{2}{l|}{RPM [1/min]} 
   & \multicolumn{2}{l|}{Voltage [V]} & \multicolumn{2}{l|}{Current [A]} &\multirow{2}{14mm}{Pin [W]}  &\multirow{2}{14mm}{ThrustEff [G/W]}  \\
\cline{2-11} 
    &    mean& std dev&   mean& std dev&   mean& std dev&    mean& std dev&  mean& std dev&         &                \\
\hline
       20 &        36.19 &        0.901 &        43.11 &        0.289 &         8233 &         87.6 &       16.675 &       0.0065 &        0.391 &       0.0140 &        6.524 &        5.547 \\
       25 &        54.59 &        0.774 &        68.57 &        0.268 &        10014 &        116.3 &       16.657 &       0.0091 &        0.622 &       0.0186 &       10.360 &        5.269 \\
       30 &        78.09 &        0.777 &        91.36 &        0.381 &        11772 &        157.1 &       16.632 &       0.0084 &        0.932 &       0.0206 &       15.494 &        5.040 \\
       35 &       101.89 &        0.824 &       121.68 &        0.569 &        13238 &        188.5 &       16.608 &       0.0076 &        1.298 &       0.0205 &       21.550 &        4.728 \\
       40 &       121.84 &        0.830 &       145.77 &        0.749 &        14480 &        169.5 &       16.576 &       0.0078 &        1.651 &       0.0263 &       27.369 &        4.452 \\
       45 &       148.23 &        0.844 &       174.95 &        0.907 &        15979 &        523.5 &       16.541 &       0.0093 &        1.943 &       0.0254 &       32.141 &        4.612 \\
       50 &       177.38 &        0.891 &       214.64 &        0.795 &        17415 &        300.2 &       16.494 &       0.0112 &        2.052 &       0.0259 &       33.843 &        5.241 \\
       55 &       209.49 &        0.896 &       254.91 &        1.193 &        18673 &        435.7 &       16.435 &       0.0111 &        2.183 &       0.0356 &       35.875 &        5.839 \\
       60 &       248.30 &        1.149 &       287.80 &        1.215 &        20116 &        556.9 &       16.372 &       0.0092 &        2.478 &       0.0411 &       40.566 &        6.121 \\
       65 &       286.57 &        1.603 &       338.44 &        2.536 &        21542 &        518.3 &       16.297 &       0.0157 &        3.087 &       0.0412 &       50.310 &        5.696 \\
       70 &       323.12 &        1.204 &       380.84 &        2.177 &        22909 &        526.4 &       16.216 &       0.0113 &        3.863 &       0.0609 &       62.637 &        5.159 \\
       75 &       360.33 &        1.595 &       432.03 &        1.998 &        24258 &        720.2 &       16.121 &       0.0118 &        5.183 &       0.0600 &       83.550 &        4.313 \\
       80 &       398.91 &        1.761 &       471.44 &        2.419 &        25330 &        403.9 &       16.013 &       0.0137 &        6.872 &       0.0843 &      110.043 &        3.625 \\
       90 &       485.15 &        3.696 &       571.83 &        6.384 &        27755 &        416.2 &       15.827 &       0.0174 &       10.574 &       0.1176 &      167.343 &        2.899 \\
      100 &       551.97 &        6.166 &       651.32 &       10.546 &        29308 &        283.0 &       15.616 &       0.0170 &       14.701 &       0.1102 &      229.564 &        2.404 \\
\hline
\end{tabular}
}

\vspace{3mm}

%%%%%%%%%%%%%%%%%%%%%%%%%%%%%%%%%%%%%%%%%%%%%%%%%%%%%%%%%%%%%%%%%%%%%%%%%%%%%%%%%%%%%%%%%%%%

\pagebreak
\noindent
{\large \bf Plots for Measurement Results:}
\vspace{5mm}

\noindent
\begin{tikzpicture}
	\begin{axis}[
		height=8cm,
		width=8cm,  %\textwidth,
		ticklabel style = {font=\tiny},
		minor tick num=4,
		ymin=0,
		grid=both,
		major grid style={gray!80},
		minor grid style={gray!25},
		xlabel={\footnotesize Motor Output [\%]},
		ylabel={\footnotesize Thrust [G]},
		legend pos=north west,
		legend style={draw=none}]
	\addplot[
		blue, mark options={black, scale=0.175},
		smooth, 
		error bars/.cd, 
		y fixed,
		y dir=both, 
		y explicit,
	] 
	table [x=out, y=th, y error=th_err, col sep=comma] {table1.dat};
	\addplot[
		red, mark options={black, scale=0.175},
		smooth, 
		error bars/.cd, 
		y fixed,
		y dir=both, 
		y explicit,
	] 
	table [x=out, y=th, y error=th_err, col sep=comma] {table2.dat};
	\end{axis}
\end{tikzpicture}
\hspace{3mm}
\begin{tikzpicture}
	\begin{axis}[
		height=8cm,
		width=8cm,  %\textwidth,
		ticklabel style = {font=\tiny},
		minor tick num=4,
		ymin=0,
		grid=both,
		major grid style={gray!80},
		minor grid style={gray!25},
		xlabel={\footnotesize Motor Output [\%]},
		ylabel={\footnotesize Torque [G cm]},
		legend pos=north west,
		legend style={draw=none}]
	\addplot[
		blue, mark options={black, scale=0.175},
		smooth, 
		error bars/.cd, 
		y fixed,
		y dir=both, 
		y explicit,
	] 
	table [x=out, y=tq, y error=tq_err, col sep=comma] {table1.dat};
	\addplot[
		red, mark options={black, scale=0.175},
		smooth, 
		error bars/.cd, 
		y fixed,
		y dir=both, 
		y explicit,
	] 
	table [x=out, y=tq, y error=tq_err, col sep=comma] {table2.dat};
	\end{axis}
\end{tikzpicture}
  
\noindent 
\vspace{2mm}
\begin{tikzpicture}
	\begin{axis}[
		height=8cm,
		width=8cm,  %\textwidth,
		ticklabel style = {font=\tiny},
		tick scale binop=\times, %base 10:-3,
		minor tick num=4,
		grid=both,
		major grid style={gray!80},
		minor grid style={gray!25},
		xlabel={\footnotesize Motor Output [\%]},
		ylabel={\footnotesize RPM [1/min]},
		legend pos=north west,
		legend style={draw=none}]
	\addplot[
		blue, mark options={black, scale=0.175},
		smooth, 
		error bars/.cd, 
			y fixed,
			y dir=both, 
			y explicit,
	] 
	table [x=out, y=rpm, y error=rpm_err, col sep=comma] {table1.dat};
	\addplot[
		red, mark options={black, scale=0.175},
		smooth, 
		error bars/.cd, 
			y fixed,
			y dir=both, 
			y explicit,
	] 
	table [x=out, y=rpm, y error=rpm_err, col sep=comma] {table2.dat};
	\end{axis}
\end{tikzpicture}
\hspace{4.65mm}
\begin{tikzpicture}
	\begin{axis}[
		height=8cm,
		width=8cm,
		ticklabel style = {font=\tiny},
		ymin=0,
		grid=both,
		xlabel={\footnotesize Motor Output [\%]},
		ylabel={\footnotesize Current [A]},
		legend pos=north west,
		legend style={draw=none}]
	\addplot[
	  blue, mark options={black, scale=0.175},
	  smooth, 
	  error bars/.cd, 
		y fixed,
		y dir=both, 
		y explicit
	] 
	table [x=out, y=a, y error=a_err, col sep=comma] {table1.dat}; \label{plot_1}
	\addplot[
	  red, mark options={black, scale=0.175},
	  smooth, 
	  error bars/.cd, 
		y fixed,
		y dir=both, 
		y explicit
	] 
	table [x=out, y=a, y error=a_err, col sep=comma] {table2.dat};
	\end{axis}
	\begin{axis}[
		height=8cm,
		width=8cm,  %\textwidth,
		axis y line*=right,
		axis x line=none,
		scaled y ticks=false,
		ticklabel style = {font=\tiny},
		grid style=dashed,
		grid=major,
		ylabel={\footnotesize Voltage [V]},
		legend style={
			nodes={scale=0.5, transform shape},
			cells={anchor=east},
			% legend pos=south east,
			at={(0.5,0.97)},anchor=north,
		}
	]
	% \addlegendimage{/pgfplots/refstyle=plot_1}\addlegendentry{Current [A]}
	\addplot[
		blue, mark options={red, scale=0.15},
		smooth,
		error bars/.cd, 
		y fixed,
		y dir=both, 
		y explicit  
	] 
	table [x=out, y=v, y error=v_err, col sep=comma] {table1.dat}; \label{plot_2}
	\addplot[
		red, mark options={red, scale=0.15},
		smooth,
		error bars/.cd, 
		y fixed,
		y dir=both, 
		y explicit  
	] 
	table [x=out, y=v, y error=v_err, col sep=comma] {table2.dat};
	% \addlegendentry{Voltage [V]}
	\end{axis}
\end{tikzpicture}
\vspace{2mm}

\noindent 
\begin{tikzpicture}
	\begin{axis}[
		height=8cm,
		width=8cm,  %\textwidth,
		ticklabel style = {font=\tiny},
		minor tick num=4,
		ymin=0,
		grid=both,
		major grid style={gray!80},
		minor grid style={gray!25},
		xlabel={\footnotesize Motor Output [\%]},
		ylabel={\footnotesize Power In [W]},
		legend pos=north west,
		legend style={
			nodes={scale=0.75, transform shape},
			cells={anchor=west},
			legend pos=north west,
		}	
	]			
	\addplot[
		blue, mark=*, mark options={blue, scale=0.5},
		smooth, 
	] 
	table [x=out, y=pin, col sep=comma] {table1.dat};
	\addplot[
		red, mark=*, mark options={red, scale=0.5},
		smooth, 
	] 
	table [x=out, y=pin, col sep=comma] {table2.dat};
	\end{axis}
	\end{tikzpicture}
\hspace{3mm}
	\begin{tikzpicture}
	\begin{axis}[
		height=8cm,
		width=8cm,  %\textwidth,
		ticklabel style = {font=\tiny},
		minor tick num=4,
		grid=both,
		major grid style={gray!80},
		minor grid style={gray!25},
		xlabel={\footnotesize Motor Output [\%]},
		ylabel={\footnotesize Thrust Efficiency [G/W]},
		legend pos=north west,
		legend style={draw=none}]
	\addplot[
		blue, mark=*, mark options={blue, scale=0.5},
		smooth, 
	] 
	table [x=out, y=theff, col sep=comma] {table1.dat};
	\addplot[
		red, mark=*, mark options={red, scale=0.5},
		smooth, 
	] 
	table [x=out, y=theff, col sep=comma] {table2.dat};
	\end{axis}
\end{tikzpicture}

%%%%%%%%%%%%%%%%%%%%%%%%%%%%%%%%%%%%%%%%%%%%%%%%%%%%%%%%%%%%%%%%%%%%%%%%%%%%%%%%%%%%%%%%%%%%

\end{document}

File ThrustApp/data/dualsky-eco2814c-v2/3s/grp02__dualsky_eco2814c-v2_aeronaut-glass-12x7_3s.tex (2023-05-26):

\documentclass[10pt]{article}

\usepackage{pgfplots}
\usepackage{multirow}
\usepackage{filecontents}

\pgfplotsset{compat=1.14}

\usepackage[margin=20mm]{geometry}

\setlength{\textheight}{240 mm}

\begin{filecontents*}{table1.dat}
out,      th,    th_err, tq,     tq_err,  rpm,   rpm_err,  v,    v_err,   a,     a_err,   pin,        theff
    2e+01,       59.05,       3.388,      155.61,      41.443,        1951,        45.0,      12.580,      0.0034,       0.665,      0.0292,       8.359,       7.065
       30,      169.89,       1.392,      334.89,      41.362,        2741,        13.2,      12.560,      0.0054,       1.406,      0.0317,      17.662,       9.619
       40,      329.78,       0.798,      632.93,      41.278,        3665,        22.3,      12.522,      0.0050,       2.998,      0.0317,      37.542,       8.784
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
       80,     1308.33,       4.292,     2367.85,      33.411,        6804,        68.1,      11.735,      0.0134,      19.135,      0.0781,     224.542,       5.827
       90,     1563.46,       4.962,     2853.03,      34.529,        7389,        60.4,      11.547,      0.0136,      25.436,      0.0934,     293.711,       5.323
      100,     1789.86,       4.983,     3285.37,      34.326,        7885,        44.8,      11.348,      0.0121,      32.216,      0.1413,     365.592,       4.896
\end{filecontents*}

\begin{filecontents*}{table4.dat}
out,      th,    th_err, tq,     tq_err,  rpm,   rpm_err,  v,    v_err,   a,     a_err,   pin,        theff
       20,       55.60,       3.723,      124.86,      70.330,        1880,        52.2,      11.983,      0.0045,       0.649,      0.0291,       7.775,       7.151
       30,      150.62,       0.936,      286.10,      70.241,        2618,        13.3,      11.968,      0.0038,       1.316,      0.0300,      15.750,       9.563
       40,      295.99,       0.877,      553.48,      70.244,        3500,        22.5,      11.933,      0.0037,       2.766,      0.0393,      33.011,       8.966
       50,      456.01,       1.188,      857.92,      70.246,        4260,        24.3,      11.879,      0.0044,       4.919,      0.0403,      58.426,       7.805
       60,      690.56,       2.310,     1267.16,      70.244,        5066,        40.0,      11.806,      0.0071,       8.291,      0.0435,      97.886,       7.055
       70,      978.17,       5.095,     1779.95,      70.270,        5958,        60.5,      11.686,      0.0072,      13.045,      0.0668,     152.450,       6.416
       80,     1273.62,       5.078,     2293.07,      70.335,        6737,        68.7,      11.548,      0.0091,      18.650,      0.0624,     215.370,       5.914
       90,     1541.85,       3.081,     2782.87,      70.395,        7347,        51.3,      11.393,      0.0094,      24.976,      0.0582,     284.565,       5.418
      100,     1761.74,       6.687,     3228.44,      71.004,        7853,        47.7,      11.218,      0.0090,      31.725,      0.2144,     355.878,       4.950
\end{filecontents*}

\begin{filecontents*}{table5.dat}
out,      th,    th_err, tq,     tq_err,  rpm,   rpm_err,  v,    v_err,   a,     a_err,   pin,        theff
       20,       54.76,       3.614,      115.21,      79.412,        1866,        50.6,      11.879,      0.0042,       0.630,      0.0286,       7.489,       7.313
       30,      147.73,       1.019,      273.10,      79.328,        2596,        12.5,      11.861,      0.0042,       1.304,      0.0221,      15.468,       9.550
       40,      289.28,       1.049,      534.78,      79.335,        3466,        18.3,      11.831,      0.0055,       2.701,      0.0312,      31.955,       9.053
       50,      449.03,       1.155,      834.73,      79.330,        4229,        24.2,      11.778,      0.0055,       4.852,      0.0390,      57.150,       7.857
       60,      677.71,       1.683,     1244.86,      79.335,        5044,        38.0,      11.695,      0.0089,       8.206,      0.0417,      95.971,       7.062
       70,      967.69,       2.307,     1742.69,      79.395,        5899,        64.9,      11.579,      0.0091,      12.885,      0.0691,     149.202,       6.486
       80,     1248.35,       7.365,     2246.33,      79.904,        6686,        66.2,      11.437,      0.0089,      18.387,      0.0918,     210.296,       5.936
       90,     1515.69,       5.962,     2737.18,      79.732,        7297,        51.0,      11.286,      0.0086,      24.603,      0.0857,     277.664,       5.459
      100,     1741.96,      11.526,     3179.97,      81.782,        7796,        47.4,      11.115,      0.0095,      31.307,      0.1693,     347.984,       5.006
\end{filecontents*}

\begin{document}

\noindent
{\large \bf Tool info}
\vspace{3mm}

\noindent
\begin{tabular}{ll}
Serial API:  & \\ 
Board:       & \\ 
Firmware:    & \\ 
Commit:      & 
\end{tabular}
\vspace{3mm}

\noindent
{\large \bf Measurement info}
\vspace{3mm}

\noindent
\begin{tabular}{ll}
Motor:        & Dualsky ECO2814C V2\\ 
KV:           & 970\\ 
Magnet poles: & 14\\ 
Propeler:     & Aerinaut Glass 12x7 fold\\ 
Blade count:  & 2\\ 
Note:         & Battery 3S 2600 mAh
\end{tabular}

\vspace{3mm}

%\noindent
%{\large \bf Measurement Results 1:}
%\vspace{3mm}

\subsection*{\large \bf Measurement Results 1:}

\noindent
\resizebox{\textwidth}{!}{
\begin{tabular}{|r|rr|rr|rr|rr|rr|r|r|}
\hline 
 \multirow[c]{2}{11mm}{Output [\%]} & \multicolumn{2}{l|}{Thrust [G]} & \multicolumn{2}{l|}{Torque [G cm]} & \multicolumn{2}{l|}{RPM [1/min]} 
   & \multicolumn{2}{l|}{Voltage [V]} & \multicolumn{2}{l|}{Current [A]} &\multirow{2}{14mm}{Pin [W]}  &\multirow{2}{14mm}{ThrustEff [G/W]}  \\
\cline{2-11} 
    &    mean& std dev&   mean& std dev&   mean& std dev&    mean& std dev&  mean& std dev&         &                \\
\hline
       20 &        59.05 &        3.388 &       155.61 &       41.443 &         1951 &         45.0 &       12.580 &       0.0034 &        0.665 &       0.0292 &        8.359 &        7.065 \\
       30 &       169.89 &        1.392 &       334.89 &       41.362 &         2741 &         13.2 &       12.560 &       0.0054 &        1.406 &       0.0317 &       17.662 &        9.619 \\
       40 &       329.78 &        0.798 &       632.93 &       41.278 &         3665 &         22.3 &       12.522 &       0.0050 &        2.998 &       0.0317 &       37.542 &        8.784 \\
       50 &       503.23 &        1.335 &       969.98 &       41.295 &         4459 &         24.6 &       12.466 &       0.0063 &        5.342 &       0.0553 &       66.598 &        7.556 \\
       60 &       740.36 &        1.963 &      1383.37 &       41.275 &         5231 &         42.2 &       12.381 &       0.0097 &        8.845 &       0.0486 &      109.513 &        6.760 \\
       70 &      1043.00 &        4.112 &      1947.29 &       41.409 &         6168 &         55.7 &       12.244 &       0.0091 &       13.888 &       0.0726 &      170.042 &        6.134 \\
       80 &      1381.31 &        4.494 &      2509.25 &       41.947 &         6988 &         63.2 &       12.078 &       0.0116 &       20.042 &       0.1080 &      242.070 &        5.706 \\
       90 &      1644.47 &        7.710 &      3017.16 &       43.223 &         7578 &         53.5 &       11.889 &       0.0111 &       26.714 &       0.1466 &      317.589 &        5.178 \\
      100 &      1902.23 &        7.706 &      3480.86 &       44.440 &         8084 &         46.7 &       11.685 &       0.0137 &       33.812 &       0.2027 &      395.105 &        4.814 \\
\hline
\end{tabular}
}

%\vspace{3mm}

%\noindent
%{\large \bf Measurement Results 2:}
%\vspace{3mm}

\subsection*{\large \bf Measurement Results 2:}

\noindent
\resizebox{\textwidth}{!}{
\begin{tabular}{|r|rr|rr|rr|rr|rr|r|r|}
\hline 
 \multirow[c]{2}{11mm}{Output [\%]} & \multicolumn{2}{l|}{Thrust [G]} & \multicolumn{2}{l|}{Torque [G cm]} & \multicolumn{2}{l|}{RPM [1/min]} 
   & \multicolumn{2}{l|}{Voltage [V]} & \multicolumn{2}{l|}{Current [A]} &\multirow{2}{14mm}{Pin [W]}  &\multirow{2}{14mm}{ThrustEff [G/W]}  \\
\cline{2-11} 
    &    mean& std dev&   mean& std dev&   mean& std dev&    mean& std dev&  mean& std dev&         &                \\
\hline
       20 &        54.79 &       13.899 &       150.24 &       38.980 &         1926 &         48.9 &       12.375 &       0.0039 &        0.660 &       0.0311 &        8.164 &        6.711 \\
       30 &       162.40 &        0.839 &       318.27 &       37.251 &         2705 &         14.7 &       12.359 &       0.0039 &        1.373 &       0.0312 &       16.970 &        9.570 \\
       40 &       319.25 &        0.891 &       610.65 &       37.257 &         3615 &         15.8 &       12.323 &       0.0058 &        2.943 &       0.0410 &       36.264 &        8.804 \\
       50 &       492.71 &        1.299 &       932.71 &       37.261 &         4382 &         21.9 &       12.268 &       0.0065 &        5.198 &       0.0414 &       63.767 &        7.727 \\
       60 &       723.29 &        3.301 &      1351.60 &       37.266 &         5195 &         45.4 &       12.175 &       0.0074 &        8.694 &       0.0473 &      105.851 &        6.833 \\
       70 &      1020.61 &        2.762 &      1884.38 &       37.383 &         6096 &         52.8 &       12.057 &       0.0089 &       13.604 &       0.0865 &      164.019 &        6.223 \\
       80 &      1335.44 &        4.103 &      2429.37 &       37.931 &         6874 &         65.3 &       11.908 &       0.0086 &       19.517 &       0.1022 &      232.405 &        5.746 \\
       90 &      1599.63 &        6.297 &      2920.87 &       38.675 &         7494 &         50.7 &       11.733 &       0.0100 &       25.976 &       0.1157 &      304.771 &        5.249 \\
      100 &      1843.81 &        9.411 &      3379.98 &       39.985 &         7981 &         49.9 &       11.545 &       0.0129 &       33.083 &       0.2150 &      381.936 &        4.828 \\
\hline
\end{tabular}
}

%\vspace{3mm}

%\noindent
%{\large \bf Measurement Results 3:}
%\vspace{3mm}

\subsection*{\large \bf Measurement Results 3:}

\noindent
\resizebox{\textwidth}{!}{
\begin{tabular}{|r|rr|rr|rr|rr|rr|r|r|}
\hline 
 \multirow[c]{2}{11mm}{Output [\%]} & \multicolumn{2}{l|}{Thrust [G]} & \multicolumn{2}{l|}{Torque [G cm]} & \multicolumn{2}{l|}{RPM [1/min]} 
   & \multicolumn{2}{l|}{Voltage [V]} & \multicolumn{2}{l|}{Current [A]} &\multirow{2}{14mm}{Pin [W]}  &\multirow{2}{14mm}{ThrustEff [G/W]}  \\
\cline{2-11} 
    &    mean& std dev&   mean& std dev&   mean& std dev&    mean& std dev&  mean& std dev&         &                \\
\hline
       20 &        57.58 &        4.216 &       142.03 &       33.204 &         1909 &         51.7 &       12.221 &       0.0035 &        0.653 &       0.0297 &        7.978 &        7.218 \\
       30 &       158.29 &        0.895 &       310.25 &       33.060 &         2667 &         14.5 &       12.206 &       0.0055 &        1.353 &       0.0386 &       16.518 &        9.583 \\
       40 &       311.32 &        0.984 &       591.73 &       33.077 &         3576 &         16.3 &       12.171 &       0.0057 &        2.878 &       0.0312 &       35.031 &        8.887 \\
       50 &       476.12 &        1.265 &       904.61 &       33.083 &         4333 &         23.8 &       12.119 &       0.0051 &        5.085 &       0.0309 &       61.621 &        7.727 \\
       60 &       708.62 &        2.072 &      1314.61 &       33.071 &         5142 &         47.4 &       12.031 &       0.0094 &        8.507 &       0.0521 &      102.350 &        6.924 \\
       70 &       996.75 &        4.141 &      1840.62 &       33.120 &         6031 &         38.7 &       11.903 &       0.0111 &       13.352 &       0.0871 &      158.922 &        6.272 \\
       80 &      1308.33 &        4.292 &      2367.85 &       33.411 &         6804 &         68.1 &       11.735 &       0.0134 &       19.135 &       0.0781 &      224.542 &        5.827 \\
       90 &      1563.46 &        4.962 &      2853.03 &       34.529 &         7389 &         60.4 &       11.547 &       0.0136 &       25.436 &       0.0934 &      293.711 &        5.323 \\
      100 &      1789.86 &        4.983 &      3285.37 &       34.326 &         7885 &         44.8 &       11.348 &       0.0121 &       32.216 &       0.1413 &      365.592 &        4.896 \\
\hline
\end{tabular}
}

%\vspace{3mm}

%\noindent
%{\large \bf Measurement Results 4:}
%\vspace{3mm}

\subsection*{\large \bf Measurement Results 4:}

\noindent
\resizebox{\textwidth}{!}{
\begin{tabular}{|r|rr|rr|rr|rr|rr|r|r|}
\hline 
 \multirow[c]{2}{11mm}{Output [\%]} & \multicolumn{2}{l|}{Thrust [G]} & \multicolumn{2}{l|}{Torque [G cm]} & \multicolumn{2}{l|}{RPM [1/min]} 
   & \multicolumn{2}{l|}{Voltage [V]} & \multicolumn{2}{l|}{Current [A]} &\multirow{2}{14mm}{Pin [W]}  &\multirow{2}{14mm}{ThrustEff [G/W]}  \\
\cline{2-11} 
    &    mean& std dev&   mean& std dev&   mean& std dev&    mean& std dev&  mean& std dev&         &                \\
\hline
       20 &        55.60 &        3.723 &       124.86 &       70.330 &         1880 &         52.2 &       11.983 &       0.0045 &        0.649 &       0.0291 &        7.775 &        7.151 \\
       30 &       150.62 &        0.936 &       286.10 &       70.241 &         2618 &         13.3 &       11.968 &       0.0038 &        1.316 &       0.0300 &       15.750 &        9.563 \\
       40 &       295.99 &        0.877 &       553.48 &       70.244 &         3500 &         22.5 &       11.933 &       0.0037 &        2.766 &       0.0393 &       33.011 &        8.966 \\
       50 &       456.01 &        1.188 &       857.92 &       70.246 &         4260 &         24.3 &       11.879 &       0.0044 &        4.919 &       0.0403 &       58.426 &        7.805 \\
       60 &       690.56 &        2.310 &      1267.16 &       70.244 &         5066 &         40.0 &       11.806 &       0.0071 &        8.291 &       0.0435 &       97.886 &        7.055 \\
       70 &       978.17 &        5.095 &      1779.95 &       70.270 &         5958 &         60.5 &       11.686 &       0.0072 &       13.045 &       0.0668 &      152.450 &        6.416 \\
       80 &      1273.62 &        5.078 &      2293.07 &       70.335 &         6737 &         68.7 &       11.548 &       0.0091 &       18.650 &       0.0624 &      215.370 &        5.914 \\
       90 &      1541.85 &        3.081 &      2782.87 &       70.395 &         7347 &         51.3 &       11.393 &       0.0094 &       24.976 &       0.0582 &      284.565 &        5.418 \\
      100 &      1761.74 &        6.687 &      3228.44 &       71.004 &         7853 &         47.7 &       11.218 &       0.0090 &       31.725 &       0.2144 &      355.878 &        4.950 \\
\hline
\end{tabular}
}

%\vspace{3mm}

%\noindent
%{\large \bf Measurement Results 5:}
%\vspace{3mm}

\subsection*{\large \bf Measurement Results 5:}

\noindent
\resizebox{\textwidth}{!}{
\begin{tabular}{|r|rr|rr|rr|rr|rr|r|r|}
\hline 
 \multirow[c]{2}{11mm}{Output [\%]} & \multicolumn{2}{l|}{Thrust [G]} & \multicolumn{2}{l|}{Torque [G cm]} & \multicolumn{2}{l|}{RPM [1/min]} 
   & \multicolumn{2}{l|}{Voltage [V]} & \multicolumn{2}{l|}{Current [A]} &\multirow{2}{14mm}{Pin [W]}  &\multirow{2}{14mm}{ThrustEff [G/W]}  \\
\cline{2-11} 
    &    mean& std dev&   mean& std dev&   mean& std dev&    mean& std dev&  mean& std dev&         &                \\
\hline
       20 &        54.76 &        3.614 &       115.21 &       79.412 &         1866 &         50.6 &       11.879 &       0.0042 &        0.630 &       0.0286 &        7.489 &        7.313 \\
       30 &       147.73 &        1.019 &       273.10 &       79.328 &         2596 &         12.5 &       11.861 &       0.0042 &        1.304 &       0.0221 &       15.468 &        9.550 \\
       40 &       289.28 &        1.049 &       534.78 &       79.335 &         3466 &         18.3 &       11.831 &       0.0055 &        2.701 &       0.0312 &       31.955 &        9.053 \\
       50 &       449.03 &        1.155 &       834.73 &       79.330 &         4229 &         24.2 &       11.778 &       0.0055 &        4.852 &       0.0390 &       57.150 &        7.857 \\
       60 &       677.71 &        1.683 &      1244.86 &       79.335 &         5044 &         38.0 &       11.695 &       0.0089 &        8.206 &       0.0417 &       95.971 &        7.062 \\
       70 &       967.69 &        2.307 &      1742.69 &       79.395 &         5899 &         64.9 &       11.579 &       0.0091 &       12.885 &       0.0691 &      149.202 &        6.486 \\
       80 &      1248.35 &        7.365 &      2246.33 &       79.904 &         6686 &         66.2 &       11.437 &       0.0089 &       18.387 &       0.0918 &      210.296 &        5.936 \\
       90 &      1515.69 &        5.962 &      2737.18 &       79.732 &         7297 &         51.0 &       11.286 &       0.0086 &       24.603 &       0.0857 &      277.664 &        5.459 \\
      100 &      1741.96 &       11.526 &      3179.97 &       81.782 &         7796 &         47.4 &       11.115 &       0.0095 &       31.307 &       0.1693 &      347.984 &        5.006 \\
\hline
\end{tabular}
}

%\vspace{3mm}

\pagebreak
%\noindent
%{\large \bf Plots for Measurement Results:}
%\vspace{3mm}

\subsection*{Plots for Measurement Results:}
%\noindent
\centerline{
\hspace{-10mm}
\begin{tikzpicture}
	\begin{axis}[
		height=8cm,
		width=8cm,  %\textwidth,
		xmin=15,
		xmax=105,
		ymin=0,
		minor x tick num=3,
		minor y tick num=3,
		ticklabel style = {font=\tiny},
		grid=both,
		major grid style={gray!80},
		minor grid style={gray!25},
		xlabel={\footnotesize Motor Output [\%]},
		ylabel={\footnotesize Thrust [G]},
		%ylabel style={ yshift = {-1mm}, },
		legend pos=north west,
		legend style={draw=none}]
	\addplot[
		blue, mark options={black, scale=0.175},
		smooth, 
		error bars/.cd, 
		y fixed,
		y dir=both, 
		y explicit,
	] 
	table [x=out, y=th, y error=th_err, col sep=comma] {table1.dat};
	\addplot[
		blue, mark options={black, scale=0.175},
		smooth, 
		error bars/.cd, 
		y fixed,
		y dir=both, 
		y explicit,
	] 
	table [x=out, y=th, y error=th_err, col sep=comma] {table2.dat};
	\addplot[
		blue, mark options={black, scale=0.175},
		smooth, 
		error bars/.cd, 
		y fixed,
		y dir=both, 
		y explicit,
	] 
	table [x=out, y=th, y error=th_err, col sep=comma] {table3.dat};
	\addplot[
		blue, mark options={black, scale=0.175},
		smooth, 
		error bars/.cd, 
		y fixed,
		y dir=both, 
		y explicit,
	] 
	table [x=out, y=th, y error=th_err, col sep=comma] {table4.dat};
	\addplot[
		blue, mark options={black, scale=0.175},
		smooth, 
		error bars/.cd, 
		y fixed,
		y dir=both, 
		y explicit,
	] 
	table [x=out, y=th, y error=th_err, col sep=comma] {table5.dat};

	\end{axis}
\end{tikzpicture}
\hspace{5mm}
\begin{tikzpicture}
	\begin{axis}[
		height=8cm,
		width=8cm,  %\textwidth,
		xmin=15,
		xmax=105,
		ymin=0,
		minor x tick num=3,
		minor y tick num=3,
		ticklabel style = {font=\tiny},
		grid=both,
		major grid style={gray!80},
		minor grid style={gray!25},
		xlabel={\footnotesize Motor Output [\%]},
		ylabel={\footnotesize Torque [G cm]},
		legend pos=north west,
		legend style={draw=none}]
	\addplot[
		blue, mark options={black, scale=0.175},
		smooth, 
		error bars/.cd, 
		y fixed,
		y dir=both, 
		y explicit,
	] 
	table [x=out, y=tq, y error=tq_err, col sep=comma] {table1.dat};
	\addplot[
		blue, mark options={black, scale=0.175},
		smooth, 
		error bars/.cd, 
		y fixed,
		y dir=both, 
		y explicit,
	] 
	table [x=out, y=tq, y error=tq_err, col sep=comma] {table2.dat};
	\addplot[
		blue, mark options={black, scale=0.175},
		smooth, 
		error bars/.cd, 
		y fixed,
		y dir=both, 
		y explicit,
	] 
	table [x=out, y=tq, y error=tq_err, col sep=comma] {table3.dat};
	\addplot[
		blue, mark options={black, scale=0.175},
		smooth, 
		error bars/.cd, 
		y fixed,
		y dir=both, 
		y explicit,
	] 
	table [x=out, y=tq, y error=tq_err, col sep=comma] {table4.dat};
	\addplot[
		blue, mark options={black, scale=0.175},
		smooth, 
		error bars/.cd, 
		y fixed,
		y dir=both, 
		y explicit,
	] 
	table [x=out, y=tq, y error=tq_err, col sep=comma] {table5.dat};

	\end{axis}
\end{tikzpicture}
}
  
%\noindent 
\centerline{
\vspace{3mm}
\begin{tikzpicture}
	\begin{axis}[
		height=8cm,
		width=8cm,  %\textwidth,
		xmin=15,
		xmax=105,
		%ymin=0,
		minor x tick num=3,
		minor y tick num=3,	
		ticklabel style = {font=\tiny},
		tick scale binop=\times, %base 10:-3,
		grid=both,
		major grid style={gray!80},
		minor grid style={gray!25},
		xlabel={\footnotesize Motor Output [\%]},
		ylabel={\footnotesize RPM [1/min]},
		legend pos=north west,
		legend style={draw=none}]
	\addplot[
		blue, mark options={black, scale=0.175},
		smooth, 
		error bars/.cd, 
			y fixed,
			y dir=both, 
			y explicit,
	] 
	table [x=out, y=rpm, y error=rpm_err, col sep=comma] {table1.dat};
	\addplot[
		blue, mark options={black, scale=0.175},
		smooth, 
		error bars/.cd, 
			y fixed,
			y dir=both, 
			y explicit,
	] 
	table [x=out, y=rpm, y error=rpm_err, col sep=comma] {table2.dat};
	\addplot[
		blue, mark options={black, scale=0.175},
		smooth, 
		error bars/.cd, 
			y fixed,
			y dir=both, 
			y explicit,
	] 
	table [x=out, y=rpm, y error=rpm_err, col sep=comma] {table3.dat};
	\addplot[
		blue, mark options={black, scale=0.175},
		smooth, 
		error bars/.cd, 
			y fixed,
			y dir=both, 
			y explicit,
	] 
	table [x=out, y=rpm, y error=rpm_err, col sep=comma] {table4.dat};
	\addplot[
		blue, mark options={black, scale=0.175},
		smooth, 
		error bars/.cd, 
			y fixed,
			y dir=both, 
			y explicit,
	] 
	table [x=out, y=rpm, y error=rpm_err, col sep=comma] {table5.dat};

	\end{axis}
\end{tikzpicture}
\hspace{4.65mm}
\begin{tikzpicture}
	\begin{axis}[
		height=8cm,
		width=8cm,
		axis y line*=right,		
		xmin=15,
		xmax=105,
		ymin=0,
		minor x tick num=3,
		ticklabel style = {font=\tiny},
		grid=both,
		xlabel={\footnotesize Motor Output [\%]},
		ylabel={\footnotesize Current [A]},
		legend pos=north west,
		legend style={draw=none}]
	\addplot[
	  blue, mark options={black, scale=0.175},
	  smooth, 
	  error bars/.cd, 
		y fixed,
		y dir=both, 
		y explicit
	] 
	table [x=out, y=a, y error=a_err, col sep=comma] {table1.dat};
	\addplot[
	  blue, mark options={black, scale=0.175},
	  smooth, 
	  error bars/.cd, 
		y fixed,
		y dir=both, 
		y explicit
	] 
	table [x=out, y=a, y error=a_err, col sep=comma] {table2.dat};
	\addplot[
	  blue, mark options={black, scale=0.175},
	  smooth, 
	  error bars/.cd, 
		y fixed,
		y dir=both, 
		y explicit
	] 
	table [x=out, y=a, y error=a_err, col sep=comma] {table3.dat};
	\addplot[
	  blue, mark options={black, scale=0.175},
	  smooth, 
	  error bars/.cd, 
		y fixed,
		y dir=both, 
		y explicit
	] 
	table [x=out, y=a, y error=a_err, col sep=comma] {table4.dat};
	\addplot[
	  blue, mark options={black, scale=0.175},
	  smooth, 
	  error bars/.cd, 
		y fixed,
		y dir=both, 
		y explicit
	] 
	table [x=out, y=a, y error=a_err, col sep=comma] {table5.dat};

	\end{axis}
	\begin{axis}[
		height=8cm,
		width=8cm,  %\textwidth,
		axis y line*=left,
		axis x line=none,
		scaled y ticks=false,
		ticklabel style = {font=\tiny},
		grid style=dashed,
		grid=major,
		ylabel={\footnotesize Voltage [V]},
		legend style={
			nodes={scale=0.5, transform shape},
			cells={anchor=east},
			% legend pos=south east,
			at={(0.5,0.97)},anchor=north,
		}
	]
%	\addlegendimage{/pgfplots/refstyle=plot_1}\addlegendentry{Current [A]}
	\addplot[
		red, mark options={red, scale=0.15},
		smooth,
		error bars/.cd, 
		y fixed,
		y dir=both, 
		y explicit  
	] 
	table [x=out, y=v, y error=v_err, col sep=comma] {table1.dat};
	\addplot[
		red, mark options={red, scale=0.15},
		smooth,
		error bars/.cd, 
		y fixed,
		y dir=both, 
		y explicit  
	] 
	table [x=out, y=v, y error=v_err, col sep=comma] {table2.dat};
	\addplot[
		red, mark options={red, scale=0.15},
		smooth,
		error bars/.cd, 
		y fixed,
		y dir=both, 
		y explicit  
	] 
	table [x=out, y=v, y error=v_err, col sep=comma] {table3.dat};
	\addplot[
		red, mark options={red, scale=0.15},
		smooth,
		error bars/.cd, 
		y fixed,
		y dir=both, 
		y explicit  
	] 
	table [x=out, y=v, y error=v_err, col sep=comma] {table4.dat};
	\addplot[
		red, mark options={red, scale=0.15},
		smooth,
		error bars/.cd, 
		y fixed,
		y dir=both, 
		y explicit  
	] 
	table [x=out, y=v, y error=v_err, col sep=comma] {table5.dat};

%	\addlegendentry{Voltage [V]}
	\end{axis}
\end{tikzpicture}
\vspace{3mm}
}

%\noindent 
\centerline{
\hspace{-10mm}
\begin{tikzpicture}
	\begin{axis}[
		height=8cm,
		width=8cm,  %\textwidth,
		xmin=15,
		xmax=105,
		ymin=0,
		minor x tick num=3,
		minor y tick num=3,		
		ticklabel style = {font=\tiny},
		grid=both,
		major grid style={gray!80},
		minor grid style={gray!25},
		xlabel={\footnotesize Motor Output [\%]},
		ylabel={\footnotesize Power In [W]},
		legend pos=north west,
		legend style={
			nodes={scale=0.75, transform shape},
			cells={anchor=west},
			legend pos=north west,
		}	
	]			
	\addplot[
		blue, mark=*, mark options={blue, scale=0.5},
		smooth, 
	] 
	table [x=out, y=pin, col sep=comma] {table1.dat};
	\addplot[
		blue, mark=*, mark options={blue, scale=0.5},
		smooth, 
	] 
	table [x=out, y=pin, col sep=comma] {table2.dat};
	\addplot[
		blue, mark=*, mark options={blue, scale=0.5},
		smooth, 
	] 
	table [x=out, y=pin, col sep=comma] {table3.dat};
	\addplot[
		blue, mark=*, mark options={blue, scale=0.5},
		smooth, 
	] 
	table [x=out, y=pin, col sep=comma] {table4.dat};
	\addplot[
		blue, mark=*, mark options={blue, scale=0.5},
		smooth, 
	] 
	table [x=out, y=pin, col sep=comma] {table5.dat};

	\end{axis}
\end{tikzpicture}
\hspace{9mm}
\begin{tikzpicture}
	\begin{axis}[
		height=8cm,
		width=8cm,  %\textwidth,
		xmin=15,
		xmax=105,
		minor x tick num=3,
		minor y tick num=3,
		ticklabel style = {font=\tiny},
		grid=both,
		major grid style={gray!80},
		minor grid style={gray!25},
		xlabel={\footnotesize Motor Output [\%]},
		ylabel={\footnotesize Thrust Efficiency [G/W]},
		legend pos=north west,
		legend style={draw=none}]
	\addplot[
		blue, mark=*, mark options={blue, scale=0.5},
		smooth, 
	] 
	table [x=out, y=theff, col sep=comma] {table1.dat};
	\addplot[
		blue, mark=*, mark options={blue, scale=0.5},
		smooth, 
	] 
	table [x=out, y=theff, col sep=comma] {table2.dat};
	\addplot[
		blue, mark=*, mark options={blue, scale=0.5},
		smooth, 
	] 
	table [x=out, y=theff, col sep=comma] {table3.dat};
	\addplot[
		blue, mark=*, mark options={blue, scale=0.5},
		smooth, 
	] 
	table [x=out, y=theff, col sep=comma] {table4.dat};
	\addplot[
		blue, mark=*, mark options={blue, scale=0.5},
		smooth, 
	] 
	table [x=out, y=theff, col sep=comma] {table5.dat};

	\end{axis}
\end{tikzpicture}
}
	
\end{document}

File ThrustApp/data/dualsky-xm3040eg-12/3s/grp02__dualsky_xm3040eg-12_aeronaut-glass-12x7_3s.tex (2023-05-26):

\documentclass[10pt]{article}

\usepackage{pgfplots}
\usepackage{multirow}
\usepackage{filecontents}

\pgfplotsset{compat=1.14}

\usepackage[margin=20mm]{geometry}

\setlength{\textheight}{240 mm}

\begin{filecontents*}{table1.dat}
out,      th,    th_err, tq,     tq_err,  rpm,   rpm_err,  v,    v_err,   a,     a_err,   pin,        theff
    2e+01,      116.33,       1.759,      244.38,      18.022,        2156,        48.2,      12.561,      0.0038,       0.908,      0.0352,      11.401,      10.204
       30,      231.20,       1.715,      427.80,      17.990,        2922,        14.8,      12.537,      0.0038,       1.790,      0.0346,      22.438,      10.304
       40,      385.68,       1.259,      711.62,      18.156,        3743,        13.4,      12.500,      0.0041,       3.417,      0.0432,      42.716,       9.029
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
       80,     1446.67,       8.127,     2610.82,      14.863,        6986,        54.2,      11.586,      0.0109,      21.705,      0.1300,     251.476,       5.753
       90,     1709.82,       8.616,     3093.89,      17.312,        7575,        38.3,      11.396,      0.0123,      28.607,      0.1396,     326.013,       5.245
      100,     1932.25,       8.805,     3542.56,      20.111,        8061,        49.6,      11.199,      0.0104,      36.072,      0.2254,     403.951,       4.783
\end{filecontents*}

\begin{filecontents*}{table4.dat}
out,      th,    th_err, tq,     tq_err,  rpm,   rpm_err,  v,    v_err,   a,     a_err,   pin,        theff
       20,      100.39,       4.352,      192.57,      13.736,        2063,        62.7,      11.919,      0.0051,       0.872,      0.0293,      10.390,       9.662
       30,      201.13,       1.566,      358.30,      13.034,        2801,        13.6,      11.901,      0.0051,       1.676,      0.0290,      19.950,      10.082
       40,      335.45,       1.496,      604.50,      13.031,        3569,        18.9,      11.866,      0.0055,       3.086,      0.0293,      36.618,       9.161
       50,      515.54,       1.446,      932.38,      13.016,        4333,        20.1,      11.811,      0.0066,       5.507,      0.0412,      65.041,       7.926
       60,      776.73,       3.085,     1355.63,      13.173,        5195,        30.7,      11.716,      0.0097,       9.450,      0.0617,     110.718,       7.015
       70,     1090.87,       2.555,     1915.36,      13.271,        6136,        49.9,      11.581,      0.0069,      14.882,      0.0744,     172.358,       6.329
       80,     1438.86,       7.572,     2478.53,      14.248,        6913,        53.2,      11.425,      0.0108,      21.276,      0.1180,     243.075,       5.919
       90,     1686.19,       7.023,     2989.78,      17.618,        7527,        37.9,      11.243,      0.0118,      28.175,      0.1452,     316.778,       5.323
      100,     1928.97,       4.754,     3437.57,      16.768,        8041,        48.1,      11.054,      0.0130,      35.493,      0.1685,     392.336,       4.917
\end{filecontents*}

\begin{filecontents*}{table5.dat}
out,      th,    th_err, tq,     tq_err,  rpm,   rpm_err,  v,    v_err,   a,     a_err,   pin,        theff
       20,      102.13,       4.573,      232.35,      17.957,        2042,        65.6,      11.762,      0.0031,       0.831,      0.0299,       9.775,      10.448
       30,      199.62,       2.057,      393.82,      17.503,        2767,        10.4,      11.748,      0.0042,       1.607,      0.0202,      18.876,      10.575
       40,      333.06,       1.823,      632.63,      17.512,        3529,        13.2,      11.715,      0.0052,       3.026,      0.0361,      35.450,       9.395
       50,      513.31,       1.819,      962.42,      17.555,        4303,        17.8,      11.656,      0.0080,       5.458,      0.0421,      63.622,       8.068
       60,      758.14,       2.018,     1420.41,      17.520,        5173,        28.3,      11.566,      0.0081,       9.420,      0.0451,     108.958,       6.958
       70,     1045.09,       2.824,     1954.28,      17.720,        6078,        55.5,      11.442,      0.0075,      14.581,      0.0583,     166.830,       6.264
       80,     1383.08,       3.068,     2487.58,      18.068,        6846,        55.5,      11.296,      0.0092,      20.766,      0.0748,     234.572,       5.896
       90,     1626.81,       5.410,     2973.42,      19.367,        7458,        49.1,      11.131,      0.0130,      27.510,      0.0969,     306.218,       5.313
      100,     1876.90,       5.003,     3439.25,      21.101,        7962,        43.9,      10.953,      0.0116,      34.941,      0.2149,     382.712,       4.904
\end{filecontents*}

\begin{document}

\noindent
{\large \bf Tool info}
\vspace{3mm}

\noindent
\begin{tabular}{ll}
Serial API:  & \\ 
Board:       & \\ 
Firmware:    & \\ 
Commit:      & 
\end{tabular}
\vspace{3mm}

\noindent
{\large \bf Measurement info}
\vspace{3mm}

\noindent
\begin{tabular}{ll}
Motor:        & Dualsky XM3040EG 12\\ 
KV:           & 1000\\ 
Magnet poles: & 14\\ 
Propeler:     & Aerinaut Glass 12x7 fold\\ 
Blade count:  & 2\\ 
Note:         & Battery 3S 2600 mAh
\end{tabular}

\vspace{3mm}

%\noindent
%{\large \bf Measurement Results 1:}
%\vspace{3mm}

\subsection*{\large \bf Measurement Results 1:}

\noindent
\resizebox{\textwidth}{!}{
\begin{tabular}{|r|rr|rr|rr|rr|rr|r|r|}
\hline 
 \multirow[c]{2}{11mm}{Output [\%]} & \multicolumn{2}{l|}{Thrust [G]} & \multicolumn{2}{l|}{Torque [G cm]} & \multicolumn{2}{l|}{RPM [1/min]} 
   & \multicolumn{2}{l|}{Voltage [V]} & \multicolumn{2}{l|}{Current [A]} &\multirow{2}{14mm}{Pin [W]}  &\multirow{2}{14mm}{ThrustEff [G/W]}  \\
\cline{2-11} 
    &    mean& std dev&   mean& std dev&   mean& std dev&    mean& std dev&  mean& std dev&         &                \\
\hline
       20 &       116.33 &        1.759 &       244.38 &       18.022 &         2156 &         48.2 &       12.561 &       0.0038 &        0.908 &       0.0352 &       11.401 &       10.204 \\
       30 &       231.20 &        1.715 &       427.80 &       17.990 &         2922 &         14.8 &       12.537 &       0.0038 &        1.790 &       0.0346 &       22.438 &       10.304 \\
       40 &       385.68 &        1.259 &       711.62 &       18.156 &         3743 &         13.4 &       12.500 &       0.0041 &        3.417 &       0.0432 &       42.716 &        9.029 \\
       50 &       566.89 &        1.287 &      1066.35 &       18.039 &         4525 &         20.4 &       12.434 &       0.0058 &        5.981 &       0.0447 &       74.361 &        7.624 \\
       60 &       834.22 &        3.110 &      1535.77 &       17.983 &         5379 &         37.1 &       12.327 &       0.0097 &       10.098 &       0.0596 &      124.477 &        6.702 \\
       70 &      1191.41 &        2.824 &      2162.04 &       18.088 &         6382 &         49.0 &       12.187 &       0.0087 &       16.080 &       0.1405 &      195.955 &        6.080 \\
       80 &      1523.22 &        5.283 &      2756.88 &       19.231 &         7219 &         66.5 &       12.008 &       0.0123 &       22.828 &       0.0983 &      274.110 &        5.557 \\
       90 &      1800.21 &        5.223 &      3270.68 &       22.341 &         7795 &         48.8 &       11.804 &       0.0124 &       30.006 &       0.1213 &      354.186 &        5.083 \\
      100 &      2047.59 &        9.965 &      3721.42 &       22.681 &         8268 &         47.8 &       11.569 &       0.0139 &       37.818 &       0.2516 &      437.532 &        4.680 \\
\hline
\end{tabular}
}

%\vspace{3mm}

%\noindent
%{\large \bf Measurement Results 2:}
%\vspace{3mm}

\subsection*{\large \bf Measurement Results 2:}

\noindent
\resizebox{\textwidth}{!}{
\begin{tabular}{|r|rr|rr|rr|rr|rr|r|r|}
\hline 
 \multirow[c]{2}{11mm}{Output [\%]} & \multicolumn{2}{l|}{Thrust [G]} & \multicolumn{2}{l|}{Torque [G cm]} & \multicolumn{2}{l|}{RPM [1/min]} 
   & \multicolumn{2}{l|}{Voltage [V]} & \multicolumn{2}{l|}{Current [A]} &\multirow{2}{14mm}{Pin [W]}  &\multirow{2}{14mm}{ThrustEff [G/W]}  \\
\cline{2-11} 
    &    mean& std dev&   mean& std dev&   mean& std dev&    mean& std dev&  mean& std dev&         &                \\
\hline
       20 &       116.88 &        3.258 &       245.36 &       16.436 &         2127 &         52.7 &       12.330 &       0.0034 &        0.886 &       0.0296 &       10.920 &       10.703 \\
       30 &       225.64 &        1.562 &       421.94 &       16.032 &         2879 &         12.8 &       12.311 &       0.0045 &        1.736 &       0.0259 &       21.366 &       10.560 \\
       40 &       372.45 &        1.472 &       690.41 &       16.021 &         3683 &         17.1 &       12.275 &       0.0038 &        3.296 &       0.0409 &       40.462 &        9.205 \\
       50 &       553.19 &        1.531 &      1036.67 &       16.044 &         4472 &         22.1 &       12.209 &       0.0057 &        5.859 &       0.0646 &       71.529 &        7.734 \\
       60 &       809.55 &        3.743 &      1505.57 &       16.048 &         5325 &         43.8 &       12.114 &       0.0087 &        9.975 &       0.0648 &      120.833 &        6.700 \\
       70 &      1148.94 &        4.910 &      2092.81 &       16.404 &         6284 &         54.3 &       11.974 &       0.0077 &       15.666 &       0.0825 &      187.573 &        6.125 \\
       80 &      1479.82 &        5.949 &      2678.17 &       17.792 &         7100 &         70.7 &       11.811 &       0.0103 &       22.246 &       0.0944 &      262.738 &        5.632 \\
       90 &      1750.55 &        4.299 &      3182.92 &       18.709 &         7683 &         54.8 &       11.624 &       0.0123 &       29.366 &       0.1300 &      341.337 &        5.129 \\
      100 &      1993.84 &        9.719 &      3641.42 &       24.967 &         8169 &         50.2 &       11.402 &       0.0138 &       37.006 &       0.2579 &      421.931 &        4.726 \\
\hline
\end{tabular}
}

%\vspace{3mm}

%\noindent
%{\large \bf Measurement Results 3:}
%\vspace{3mm}

\subsection*{\large \bf Measurement Results 3:}

\noindent
\resizebox{\textwidth}{!}{
\begin{tabular}{|r|rr|rr|rr|rr|rr|r|r|}
\hline 
 \multirow[c]{2}{11mm}{Output [\%]} & \multicolumn{2}{l|}{Thrust [G]} & \multicolumn{2}{l|}{Torque [G cm]} & \multicolumn{2}{l|}{RPM [1/min]} 
   & \multicolumn{2}{l|}{Voltage [V]} & \multicolumn{2}{l|}{Current [A]} &\multirow{2}{14mm}{Pin [W]}  &\multirow{2}{14mm}{ThrustEff [G/W]}  \\
\cline{2-11} 
    &    mean& std dev&   mean& std dev&   mean& std dev&    mean& std dev&  mean& std dev&         &                \\
\hline
       20 &       113.14 &        4.042 &       243.49 &       14.103 &         2094 &         59.7 &       12.150 &       0.0042 &        0.854 &       0.0201 &       10.376 &       10.904 \\
       30 &       215.70 &        1.835 &       413.79 &       13.145 &         2844 &         10.3 &       12.131 &       0.0046 &        1.695 &       0.0201 &       20.562 &       10.490 \\
       40 &       359.00 &        1.649 &       675.05 &       13.159 &         3641 &         21.0 &       12.088 &       0.0051 &        3.220 &       0.0298 &       38.924 &        9.223 \\
       50 &       536.75 &        1.902 &      1012.20 &       13.275 &         4411 &         21.2 &       12.026 &       0.0062 &        5.712 &       0.0568 &       68.689 &        7.814 \\
       60 &       790.52 &        1.903 &      1475.67 &       13.186 &         5271 &         32.8 &       11.918 &       0.0121 &        9.762 &       0.0505 &      116.342 &        6.795 \\
       70 &      1110.08 &        4.988 &      2041.59 &       13.657 &         6210 &         52.3 &       11.768 &       0.0126 &       15.246 &       0.0851 &      179.422 &        6.187 \\
       80 &      1446.67 &        8.127 &      2610.82 &       14.863 &         6986 &         54.2 &       11.586 &       0.0109 &       21.705 &       0.1300 &      251.476 &        5.753 \\
       90 &      1709.82 &        8.616 &      3093.89 &       17.312 &         7575 &         38.3 &       11.396 &       0.0123 &       28.607 &       0.1396 &      326.013 &        5.245 \\
      100 &      1932.25 &        8.805 &      3542.56 &       20.111 &         8061 &         49.6 &       11.199 &       0.0104 &       36.072 &       0.2254 &      403.951 &        4.783 \\
\hline
\end{tabular}
}

%\vspace{3mm}

%\noindent
%{\large \bf Measurement Results 4:}
%\vspace{3mm}

\subsection*{\large \bf Measurement Results 4:}

\noindent
\resizebox{\textwidth}{!}{
\begin{tabular}{|r|rr|rr|rr|rr|rr|r|r|}
\hline 
 \multirow[c]{2}{11mm}{Output [\%]} & \multicolumn{2}{l|}{Thrust [G]} & \multicolumn{2}{l|}{Torque [G cm]} & \multicolumn{2}{l|}{RPM [1/min]} 
   & \multicolumn{2}{l|}{Voltage [V]} & \multicolumn{2}{l|}{Current [A]} &\multirow{2}{14mm}{Pin [W]}  &\multirow{2}{14mm}{ThrustEff [G/W]}  \\
\cline{2-11} 
    &    mean& std dev&   mean& std dev&   mean& std dev&    mean& std dev&  mean& std dev&         &                \\
\hline
       20 &       100.39 &        4.352 &       192.57 &       13.736 &         2063 &         62.7 &       11.919 &       0.0051 &        0.872 &       0.0293 &       10.390 &        9.662 \\
       30 &       201.13 &        1.566 &       358.30 &       13.034 &         2801 &         13.6 &       11.901 &       0.0051 &        1.676 &       0.0290 &       19.950 &       10.082 \\
       40 &       335.45 &        1.496 &       604.50 &       13.031 &         3569 &         18.9 &       11.866 &       0.0055 &        3.086 &       0.0293 &       36.618 &        9.161 \\
       50 &       515.54 &        1.446 &       932.38 &       13.016 &         4333 &         20.1 &       11.811 &       0.0066 &        5.507 &       0.0412 &       65.041 &        7.926 \\
       60 &       776.73 &        3.085 &      1355.63 &       13.173 &         5195 &         30.7 &       11.716 &       0.0097 &        9.450 &       0.0617 &      110.718 &        7.015 \\
       70 &      1090.87 &        2.555 &      1915.36 &       13.271 &         6136 &         49.9 &       11.581 &       0.0069 &       14.882 &       0.0744 &      172.358 &        6.329 \\
       80 &      1438.86 &        7.572 &      2478.53 &       14.248 &         6913 &         53.2 &       11.425 &       0.0108 &       21.276 &       0.1180 &      243.075 &        5.919 \\
       90 &      1686.19 &        7.023 &      2989.78 &       17.618 &         7527 &         37.9 &       11.243 &       0.0118 &       28.175 &       0.1452 &      316.778 &        5.323 \\
      100 &      1928.97 &        4.754 &      3437.57 &       16.768 &         8041 &         48.1 &       11.054 &       0.0130 &       35.493 &       0.1685 &      392.336 &        4.917 \\
\hline
\end{tabular}
}

%\vspace{3mm}

%\noindent
%{\large \bf Measurement Results 5:}
%\vspace{3mm}

\subsection*{\large \bf Measurement Results 5:}

\noindent
\resizebox{\textwidth}{!}{
\begin{tabular}{|r|rr|rr|rr|rr|rr|r|r|}
\hline 
 \multirow[c]{2}{11mm}{Output [\%]} & \multicolumn{2}{l|}{Thrust [G]} & \multicolumn{2}{l|}{Torque [G cm]} & \multicolumn{2}{l|}{RPM [1/min]} 
   & \multicolumn{2}{l|}{Voltage [V]} & \multicolumn{2}{l|}{Current [A]} &\multirow{2}{14mm}{Pin [W]}  &\multirow{2}{14mm}{ThrustEff [G/W]}  \\
\cline{2-11} 
    &    mean& std dev&   mean& std dev&   mean& std dev&    mean& std dev&  mean& std dev&         &                \\
\hline
       20 &       102.13 &        4.573 &       232.35 &       17.957 &         2042 &         65.6 &       11.762 &       0.0031 &        0.831 &       0.0299 &        9.775 &       10.448 \\
       30 &       199.62 &        2.057 &       393.82 &       17.503 &         2767 &         10.4 &       11.748 &       0.0042 &        1.607 &       0.0202 &       18.876 &       10.575 \\
       40 &       333.06 &        1.823 &       632.63 &       17.512 &         3529 &         13.2 &       11.715 &       0.0052 &        3.026 &       0.0361 &       35.450 &        9.395 \\
       50 &       513.31 &        1.819 &       962.42 &       17.555 &         4303 &         17.8 &       11.656 &       0.0080 &        5.458 &       0.0421 &       63.622 &        8.068 \\
       60 &       758.14 &        2.018 &      1420.41 &       17.520 &         5173 &         28.3 &       11.566 &       0.0081 &        9.420 &       0.0451 &      108.958 &        6.958 \\
       70 &      1045.09 &        2.824 &      1954.28 &       17.720 &         6078 &         55.5 &       11.442 &       0.0075 &       14.581 &       0.0583 &      166.830 &        6.264 \\
       80 &      1383.08 &        3.068 &      2487.58 &       18.068 &         6846 &         55.5 &       11.296 &       0.0092 &       20.766 &       0.0748 &      234.572 &        5.896 \\
       90 &      1626.81 &        5.410 &      2973.42 &       19.367 &         7458 &         49.1 &       11.131 &       0.0130 &       27.510 &       0.0969 &      306.218 &        5.313 \\
      100 &      1876.90 &        5.003 &      3439.25 &       21.101 &         7962 &         43.9 &       10.953 &       0.0116 &       34.941 &       0.2149 &      382.712 &        4.904 \\
\hline
\end{tabular}
}

%\vspace{3mm}

\pagebreak
%\noindent
%{\large \bf Plots for Measurement Results:}
%\vspace{3mm}

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

%	\addlegendentry{Voltage [V]}
	\end{axis}
\end{tikzpicture}
\vspace{3mm}
}

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

	\end{axis}
\end{tikzpicture}
}
	
\end{document}

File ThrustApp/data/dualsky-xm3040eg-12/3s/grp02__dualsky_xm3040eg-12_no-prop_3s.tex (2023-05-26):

\documentclass[10pt]{article}

\usepackage{pgfplots}
\usepackage{multirow}
\usepackage{filecontents}

\pgfplotsset{compat=1.14}

\usepackage[margin=20mm]{geometry}

\setlength{\textheight}{240 mm}

\begin{filecontents*}{table1.dat}
out,      th,    th_err, tq,     tq_err,  rpm,   rpm_err,  v,    v_err,   a,     a_err,   pin,        theff
    2e+01,       -0.32,       2.017,        2.02,       2.778,        6071,        23.6,      12.572,      0.0040,       0.528,      0.0310,       6.640,      -0.048
       30,       -0.29,       2.017,        4.72,       2.754,        8117,        37.4,      12.563,      0.0038,       0.789,      0.0300,       9.909,      -0.030
       40,       -0.28,       2.017,        5.48,       2.752,        9330,        21.1,      12.556,      0.0031,       0.953,      0.0221,      11.962,      -0.023
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
       80,        0.04,       0.094,        8.83,       3.200,       11553,        26.9,      12.501,      0.0031,       1.150,      0.0292,      14.381,       0.003
       90,        0.07,       0.094,        8.94,       3.200,       11806,        21.6,      12.501,      0.0043,       1.181,      0.0296,      14.763,       0.005
      100,        0.12,       0.093,        8.64,       3.203,       12561,        41.7,      12.498,      0.0056,       1.224,      0.1010,      15.300,       0.008
\end{filecontents*}

\begin{filecontents*}{table4.dat}
out,      th,    th_err, tq,     tq_err,  rpm,   rpm_err,  v,    v_err,   a,     a_err,   pin,        theff
       20,       -0.09,       0.126,        9.04,       1.601,        6280,        29.2,      12.517,      0.0038,       0.512,      0.0281,       6.409,      -0.015
       30,       -0.16,       0.124,       10.04,       1.591,        8333,        36.6,      12.511,      0.0037,       0.763,      0.0189,       9.548,      -0.017
       40,       -0.12,       0.125,        9.72,       1.584,        9503,        18.4,      12.502,      0.0030,       0.904,      0.0257,      11.307,      -0.011
       50,       -0.07,       0.124,        9.55,       1.582,       10260,        26.8,      12.500,      0.0040,       0.978,      0.0245,      12.226,      -0.006
       60,       -0.03,       0.124,        9.32,       1.582,       10846,        27.1,      12.494,      0.0039,       1.053,      0.0290,      13.156,      -0.002
       70,       -0.00,       0.125,        9.16,       1.581,       11292,        23.0,      12.492,      0.0035,       1.123,      0.0426,      14.025,      -0.000
       80,        0.05,       0.125,        9.61,       1.581,       11570,        27.3,      12.489,      0.0051,       1.143,      0.0289,      14.271,       0.003
       90,        0.08,       0.131,        9.68,       1.587,       11814,        23.1,      12.484,      0.0042,       1.182,      0.0290,      14.750,       0.006
      100,        0.13,       0.126,        9.59,       1.585,       12563,        40.2,      12.483,      0.0041,       1.185,      0.1048,      14.793,       0.009
\end{filecontents*}

\begin{filecontents*}{table5.dat}
out,      th,    th_err, tq,     tq_err,  rpm,   rpm_err,  v,    v_err,   a,     a_err,   pin,        theff
       20,       -0.15,       0.120,        8.38,       1.288,        6312,        31.6,      12.500,      0.0048,       0.489,      0.0272,       6.106,      -0.024
       30,       -0.14,       0.121,        9.49,       1.240,        8371,        37.7,      12.493,      0.0031,       0.744,      0.0296,       9.300,      -0.015
       40,       -0.09,       0.120,        9.13,       1.235,        9542,        22.7,      12.486,      0.0021,       0.883,      0.0286,      11.025,      -0.008
       50,       -0.10,       0.121,        9.31,       1.234,       10302,        24.1,      12.483,      0.0035,       0.968,      0.0294,      12.082,      -0.009
       60,       -0.08,       0.119,        9.11,       1.235,       10876,        30.6,      12.480,      0.0037,       1.059,      0.0289,      13.218,      -0.006
       70,       -0.06,       0.120,        9.13,       1.238,       11306,        27.7,      12.472,      0.0033,       1.095,      0.0296,      13.660,      -0.005
       80,       -0.04,       0.120,        9.46,       1.233,       11583,        35.2,      12.472,      0.0037,       1.136,      0.0293,      14.172,      -0.003
       90,       -0.04,       0.122,        9.61,       1.239,       11839,        28.9,      12.469,      0.0033,       1.163,      0.0197,      14.502,      -0.003
      100,       -0.04,       0.125,        9.56,       1.252,       12562,        44.2,      12.465,      0.0039,       1.205,      0.1231,      15.016,      -0.003
\end{filecontents*}

\begin{document}

\noindent
{\large \bf Tool info}
\vspace{3mm}

\noindent
\begin{tabular}{ll}
Serial API:  & \\ 
Board:       & \\ 
Firmware:    & \\ 
Commit:      & 
\end{tabular}
\vspace{3mm}

\noindent
{\large \bf Measurement info}
\vspace{3mm}

\noindent
\begin{tabular}{ll}
Motor:        & Dualsky XM3040EG-12\\ 
KV:           & 1000\\ 
Magnet poles: & 14\\ 
Propeler:     & no prop\\ 
Blade count:  & 2\\ 
Note:         & Battery 3S 2600mAh
\end{tabular}

\vspace{3mm}

%\noindent
%{\large \bf Measurement Results 1:}
%\vspace{3mm}

\subsection*{\large \bf Measurement Results 1:}

\noindent
\resizebox{\textwidth}{!}{
\begin{tabular}{|r|rr|rr|rr|rr|rr|r|r|}
\hline 
 \multirow[c]{2}{11mm}{Output [\%]} & \multicolumn{2}{l|}{Thrust [G]} & \multicolumn{2}{l|}{Torque [G cm]} & \multicolumn{2}{l|}{RPM [1/min]} 
   & \multicolumn{2}{l|}{Voltage [V]} & \multicolumn{2}{l|}{Current [A]} &\multirow{2}{14mm}{Pin [W]}  &\multirow{2}{14mm}{ThrustEff [G/W]}  \\
\cline{2-11} 
    &    mean& std dev&   mean& std dev&   mean& std dev&    mean& std dev&  mean& std dev&         &                \\
\hline
       20 &        -0.32 &        2.017 &         2.02 &        2.778 &         6071 &         23.6 &       12.572 &       0.0040 &        0.528 &       0.0310 &        6.640 &       -0.048 \\
       30 &        -0.29 &        2.017 &         4.72 &        2.754 &         8117 &         37.4 &       12.563 &       0.0038 &        0.789 &       0.0300 &        9.909 &       -0.030 \\
       40 &        -0.28 &        2.017 &         5.48 &        2.752 &         9330 &         21.1 &       12.556 &       0.0031 &        0.953 &       0.0221 &       11.962 &       -0.023 \\
       50 &        -0.26 &        2.017 &         5.52 &        2.750 &        10125 &         27.4 &       12.555 &       0.0039 &        1.053 &       0.0296 &       13.222 &       -0.020 \\
       60 &        -0.30 &        2.017 &         5.86 &        2.750 &        10730 &         23.4 &       12.548 &       0.0050 &        1.111 &       0.0311 &       13.937 &       -0.022 \\
       70 &        -0.31 &        2.017 &         6.19 &        2.750 &        11208 &         26.4 &       12.542 &       0.0048 &        1.176 &       0.0393 &       14.749 &       -0.021 \\
       80 &        -0.24 &        2.017 &         6.34 &        2.754 &        11493 &         25.8 &       12.542 &       0.0043 &        1.219 &       0.0386 &       15.291 &       -0.016 \\
       90 &        -0.22 &        2.017 &         6.61 &        2.750 &        11763 &         34.4 &       12.536 &       0.0031 &        1.239 &       0.0313 &       15.532 &       -0.014 \\
      100 &        -0.16 &        2.017 &         6.63 &        2.755 &        12522 &         41.0 &       12.531 &       0.0049 &        1.297 &       0.1546 &       16.250 &       -0.010 \\
\hline
\end{tabular}
}

%\vspace{3mm}

%\noindent
%{\large \bf Measurement Results 2:}
%\vspace{3mm}

\subsection*{\large \bf Measurement Results 2:}
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

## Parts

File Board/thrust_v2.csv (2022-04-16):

Source: | C:\scratch\Stm32\hardware\KiProjects\thrust_v2_mod3\thrust_v2.sch
Date: | 22/05/2021 20:00
Tool: | Eeschema (5.1.9)-1
Generator: | C:\Program Files\KiCad\bin\scripting\plugins/bom_csv_grouped_by_value_with_fp.py
Component Count: | 187
Ref | Qnty | Value | Cmp name | Footprint | Description | Vendor
C1, C2, C22, C38, C41, C42, C48, | 7 | 10nF | C_Small | Capacitor_SMD:C_0603_1608Metric_Pad1.08x0.95mm_HandSolder | Unpolarized capacitor, small symbol
C3, C18, C49, | 3 | 1uF | C_Small | Capacitor_SMD:C_0603_1608Metric_Pad1.08x0.95mm_HandSolder | Unpolarized capacitor, small symbol
C4, C17, | 2 | 10uF/6.3V | CP_Small | priv:CP_EIA-3528-21_Kemet-B_Pad1.50x2.35mm_HandSolder | Polarized capacitor, small symbol
C5, C6, C7, C10, C13, C16, C19, C20, C21, C23, C24, C25, C26, C28, C29, C30, C32, C36, C59, C60, C61, C62, C69, | 23 | 100nF | C_Small | Capacitor_SMD:C_0603_1608Metric_Pad1.08x0.95mm_HandSolder | Unpolarized capacitor, small symbol
C8, C9, C11, C12, C14, C15, C27, | 7 | 10uF | C_Small | Capacitor_SMD:C_0603_1608Metric_Pad1.08x0.95mm_HandSolder | Unpolarized capacitor, small symbol
C31, C37, | 2 | 2.2uF | C_Small | Capacitor_SMD:C_0603_1608Metric_Pad1.08x0.95mm_HandSolder | Unpolarized capacitor, small symbol
C33, C35, | 2 | 10pF | C_Small | Capacitor_SMD:C_0603_1608Metric_Pad1.08x0.95mm_HandSolder | Unpolarized capacitor, small symbol
C34, | 1 | 22nF | C_Small | Capacitor_SMD:C_0603_1608Metric_Pad1.08x0.95mm_HandSolder | Unpolarized capacitor, small symbol
C39, | 1 | 47uF/10V | CP_Small | priv:CP_EIA-3528-21_Kemet-B_Pad1.50x2.35mm_HandSolder | Polarized capacitor, small symbol
C40, C66, | 2 | 68p | C_Small | Capacitor_SMD:C_0603_1608Metric_Pad1.08x0.95mm_HandSolder | Unpolarized capacitor, small symbol
C43, | 1 | 680p | C_Small | Capacitor_SMD:C_0603_1608Metric_Pad1.08x0.95mm_HandSolder | Unpolarized capacitor, small symbol
C44, C45, | 2 | 20pF | C_Small | Capacitor_SMD:C_0603_1608Metric_Pad1.08x0.95mm_HandSolder | Unpolarized capacitor, small symbol
C46, C47, | 2 | 6.8pF | C_Small | Capacitor_SMD:C_0603_1608Metric_Pad1.08x0.95mm_HandSolder | Unpolarized capacitor, small symbol
C50, C53, C56, | 3 | 220nF | C_Small | Capacitor_SMD:C_0603_1608Metric_Pad1.08x0.95mm_HandSolder | Unpolarized capacitor, small symbol
C51, C63, | 2 | 4.7uF | C_Small | Capacitor_SMD:C_0603_1608Metric_Pad1.08x0.95mm_HandSolder | Unpolarized capacitor, small symbol
C52, C57, C58, | 3 | 22pF | C_Small | Capacitor_SMD:C_0603_1608Metric_Pad1.08x0.95mm_HandSolder | Unpolarized capacitor, small symbol
C64, C65, | 2 | 47pF | C_Small | Capacitor_SMD:C_0603_1608Metric_Pad1.08x0.95mm_HandSolder | Unpolarized capacitor, small symbol
D1, D7, D8, | 3 | B340A-13-F | D_Schottky | priv:D_SMA | Schottky diode
D2, | 1 | LED_RED | LED | LED_SMD:LED_0603_1608Metric_Pad1.05x0.95mm_HandSolder | Light emitting diode
D4, | 1 | LED_BLUE | LED | LED_SMD:LED_0603_1608Metric_Pad1.05x0.95mm_HandSolder | Light emitting diode
D5, | 1 | LED_YELLOW | LED | LED_SMD:LED_0603_1608Metric_Pad1.05x0.95mm_HandSolder | Light emitting diode
D6, | 1 | LED_GREEN | LED | LED_SMD:LED_0603_1608Metric_Pad1.05x0.95mm_HandSolder | Light emitting diode
F1, | 1 | Dioda: prostownicza Schottky; SMD; 40V; 3A; SMA; 850mW | Polyfuse_Small | Fuse:Fuse_0805_2012Metric_Pad1.15x1.40mm_HandSolder | Resettable fuse, polymeric positive temperature coefficient, small symbol
J1, J2, J3, J7, | 4 | Conn_01x05 | Conn_01x05 | Connector_PinHeader_2.54mm:PinHeader_1x05_P2.54mm_Vertical | Generic connector, single row, 01x05, script generated (kicad-library-utils/schlib/autogen/connector/)
J4, | 1 | Conn_3.3V | Conn_01x02 | Connector_PinHeader_2.54mm:PinHeader_1x02_P2.54mm_Vertical | Generic connector, single row, 01x02, script generated (kicad-library-utils/schlib/autogen/connector/)
J5, | 1 | Conn_3.3VA | Conn_01x02 | Connector_PinHeader_2.54mm:PinHeader_1x02_P2.54mm_Vertical | Generic connector, single row, 01x02, script generated (kicad-library-utils/schlib/autogen/connector/)
J8, | 1 | Ext_5V | Conn_01x02 | Connector_PinHeader_2.54mm:PinHeader_1x02_P2.54mm_Vertical | Generic connector, single row, 01x02, script generated (kicad-library-utils/schlib/autogen/connector/)
J10, | 1 | BattVolt | Conn_01x02 | Connector_PinHeader_2.54mm:PinHeader_1x02_P2.54mm_Vertical | Generic connector, single row, 01x02, script generated (kicad-library-utils/schlib/autogen/connector/)
J12, | 1 | MX-67068-9000(USB-B) | USB_B | priv:USB_B_OST_USB-B1HSxx_Horizontal_mod | USB Type B connector
J13, | 1 | Conn_SWD | Conn_01x06 | Connector_PinHeader_2.54mm:PinHeader_1x06_P2.54mm_Vertical | Generic connector, single row, 01x06, script generated (kicad-library-utils/schlib/autogen/connector/)
J14, | 1 | Motor | Conn_01x03 | Connector_PinHeader_2.54mm:PinHeader_1x03_P2.54mm_Vertical | Generic connector, single row, 01x03, script generated (kicad-library-utils/schlib/autogen/connector/)
J15, | 1 | BattCurr | Conn_01x05 | Connector_PinHeader_2.54mm:PinHeader_1x05_P2.54mm_Vertical | Generic connector, single row, 01x05, script generated (kicad-library-utils/schlib/autogen/connector/)
J16, | 1 | SensorRPM | Conn_01x03 | Connector_PinHeader_2.54mm:PinHeader_1x03_P2.54mm_Vertical | Generic connector, single row, 01x03, script generated (kicad-library-utils/schlib/autogen/connector/)
J17, | 1 | UART/I2C | Conn_01x04 | Connector_PinHeader_2.54mm:PinHeader_1x04_P2.54mm_Vertical | Generic connector, single row, 01x04, script generated (kicad-library-utils/schlib/autogen/connector/)
JP1, JP2, | 2 | closed | Jumper_NC_Small | Jumper:SolderJumper-2_P1.3mm_Open_TrianglePad1.0x1.5mm | Jumper, normally closed, small symbol
L1, L2, L3, | 3 | 3.3uH | L_Small | Inductor_SMD:L_0603_1608Metric_Pad1.05x0.95mm_HandSolder | Inductor, small symbol
L4, L5, L7, | 3 | f.bead BLM18PG471SH1D | L_Small | Inductor_SMD:L_0603_1608Metric_Pad1.05x0.95mm_HandSolder | Inductor, small symbol
LG1, | 1 | Logo_1 | Logo_1 | priv:LOGO_QX4_knot_circ2_24mm | QQ logo, large
M1, M2, M3, M4, | 4 | Mounting_Hole | Mounting_Hole | MountingHole:MountingHole_3.2mm_M3
Q1, Q2, Q3, | 3 | MMBT4403 | MMBT4403 | Package_TO_SOT_SMD:SOT-23 | Tranzystor: PNP; bipolarny; 40V; 600mA; SOT23
R1, R2, R3, R4, R5, R6, | 6 | 100 | R_Small | Resistor_SMD:R_0603_1608Metric_Pad0.98x0.95mm_HandSolder | Resistor, small symbol
R7, R9, R11, | 3 | 12k | R_Small | Resistor_SMD:R_0603_1608Metric_Pad0.98x0.95mm_HandSolder | Resistor, small symbol
R8, R10, R12, | 3 | 8.2k | R_Small | Resistor_SMD:R_0603_1608Metric_Pad0.98x0.95mm_HandSolder | Resistor, small symbol
R13, | 1 | infty | R_Small | Resistor_SMD:R_0603_1608Metric_Pad0.98x0.95mm_HandSolder | Resistor, small symbol
R14, R33, R38, R47, | 4 | 10k | R_Small | Resistor_SMD:R_0603_1608Metric_Pad0.98x0.95mm_HandSolder | Resistor, small symbol
R15, R20, R27, R37, | 4 | 1k | R_Small | Resistor_SMD:R_0603_1608Metric_Pad0.98x0.95mm_HandSolder | Resistor, small symbol
R16, | 1 | 100k | R_Small | Resistor_SMD:R_0603_1608Metric_Pad0.98x0.95mm_HandSolder | Resistor, small symbol
R17, R18, R39, R40, | 4 | 4.7k | R_Small | Resistor_SMD:R_0603_1608Metric_Pad0.98x0.95mm_HandSolder | Resistor, small symbol
R19, R21, R22, R29, R30, R45, | 6 | 220 | R_Small | Resistor_SMD:R_0603_1608Metric_Pad0.98x0.95mm_HandSolder | Resistor, small symbol
R23, R25, R26, R28, | 4 | 330 | R_Small | Resistor_SMD:R_0603_1608Metric_Pad0.98x0.95mm_HandSolder | Resistor, small symbol
R24, | 1 | 50 | R_Small | Resistor_SMD:R_0603_1608Metric_Pad0.98x0.95mm_HandSolder | Resistor, small symbol
R34, R35, R36, | 3 | 680 | R_Small | Resistor_SMD:R_0603_1608Metric_Pad0.98x0.95mm_HandSolder | Resistor, small symbol
R41, | 1 | 47k | R_Small | Resistor_SMD:R_0603_1608Metric_Pad0.98x0.95mm_HandSolder | Resistor, small symbol
R42, | 1 | 68k | R_Small | Resistor_SMD:R_0603_1608Metric_Pad0.98x0.95mm_HandSolder | Resistor, small symbol
R43, R44, | 2 | 22 | R_Small | Resistor_SMD:R_0603_1608Metric_Pad0.98x0.95mm_HandSolder | Resistor, small symbol
SW2, | 1 | BootBtn | SW_Push_SH | priv:SW_Push_1P1T-SH_NO_CK_KMR2xxG | Push button switch, generic, two pins
SW4, | 1 | UserBtn | SW_Push_GND2 | priv:SW_SPST_Panasonic_EVQPL_3PL_5PL_PT_A15 | Push button switch, generic, two pins
SW5, | 1 | ResetBtn | SW_Push_SH | priv:SW_Push_1P1T-SH_NO_CK_KMR2xxG | Push button switch, generic, two pins
TP1, TP3, TP9, TP14, TP16, TP17, TP18, TP19, TP20, TP21, | 10 | TestPoint | TestPoint | TestPoint:TestPoint_Pad_1.5x1.5mm | test point
TP2, | 1 | MCO2 | TestPoint | TestPoint:TestPoint_Pad_1.5x1.5mm | test point
TP4, TP5, TP6, TP25, | 4 | TestPoint | TestPoint | TestPoint:TestPoint_Pad_D1.0mm | test point
TP7, | 1 | SCK | TestPoint | TestPoint:TestPoint_Pad_1.5x1.5mm | test point
TP8, | 1 | Data1 | TestPoint | TestPoint:TestPoint_Pad_1.5x1.5mm | test point
TP10, | 1 | Rate | TestPoint | TestPoint:TestPoint_Pad_1.5x1.5mm | test point
TP11, | 1 | Data2 | TestPoint | TestPoint:TestPoint_Pad_1.5x1.5mm | test point
TP12, | 1 | Data3 | TestPoint | TestPoint:TestPoint_Pad_1.5x1.5mm | test point
TP13, | 1 | 3.3V | TestPoint | TestPoint:TestPoint_Pad_1.5x1.5mm | test point
TP15, | 1 | GND | TestPoint | TestPoint:TestPoint_Pad_1.5x1.5mm | test point
TP22, | 1 | PC13 | TestPoint | TestPoint:TestPoint_Pad_1.5x1.5mm | test point
TP23, | 1 | UserBtn GND | TestPoint | TestPoint:TestPoint_Pad_1.5x1.5mm | test point
TP24, | 1 | UserBtn 3V3 | TestPoint | TestPoint:TestPoint_Pad_1.5x1.5mm | test point
TP26, | 1 | PC6 | TestPoint | TestPoint:TestPoint_Pad_1.5x1.5mm | test point
U1, | 1 | NCP1117-3.3/LDI1117-3.3H | NCP1117-3.3_SOT223 | Package_TO_SOT_SMD:SOT-223-3_TabPin2 | 1A Low drop-out regulator, Fixed Output 3.3V, SOT-223
U2, | 1 | MIC5504-3.3YM5 | MIC5504-3.3YM5 | priv:SOT-23-5 | 300mA Low-dropout Voltage Regulator, Vout 3.3V, Vin up to 5.5V, SOT-23
U3, U4, U5, | 3 | HX711 | HX711 | Package_SO:SOIC-16_3.9x9.9mm_P1.27mm | 24-Bit Analog-to-Digital Converter (ADC) for Weigh Scales
U6, | 1 | USBLC6-2P6 | USBLC6-2P6 | priv:SOT-23-6 | Very low capacitance ESD protection diode, 2 data-line, SOT-666
U7, | 1 | MCP1501_SOT23 | MCP1501_SOT23 | priv:SOT-23-6 | high precision voltage reference
U8, | 1 | LCD_SSD1306_I2C | LCD_SSD1306_I2C | Connector_PinHeader_2.54mm:PinHeader_1x04_P2.54mm_Vertical | OLED LCD 128x64 - SSD1306
U12, | 1 | STM32F401RETx | STM32F401RETx | Package_QFP:LQFP-64_10x10mm_P0.5mm | ARM Cortex-M4 MCU, 512KB flash, 96KB RAM, 84MHz, 1.7-3.6V, 50 GPIO, LQFP-64
Y1, | 1 | 8MHz | Crystal_Small | Crystal:Crystal_HC49-4H_Vertical | Two pin crystal, small symbol
Y2, | 1 | 32.768kHz | Crystal_Small | priv:ABS25 | Two pin crystal, small symbol

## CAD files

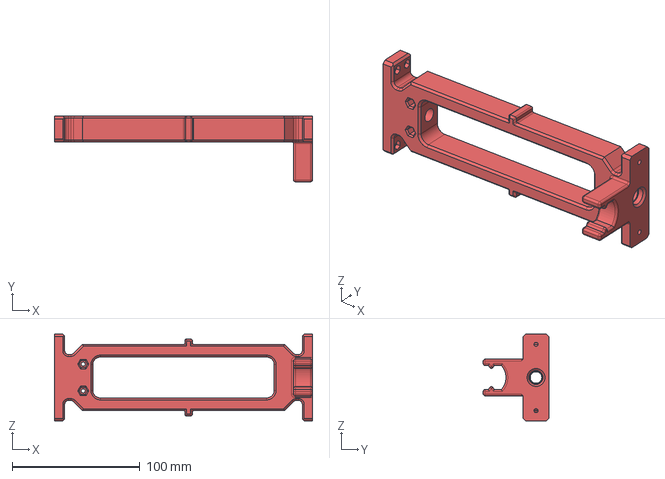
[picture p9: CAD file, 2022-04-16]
Tool/th3 spindle.step
202.0 x 51.4 x 68.0 mm

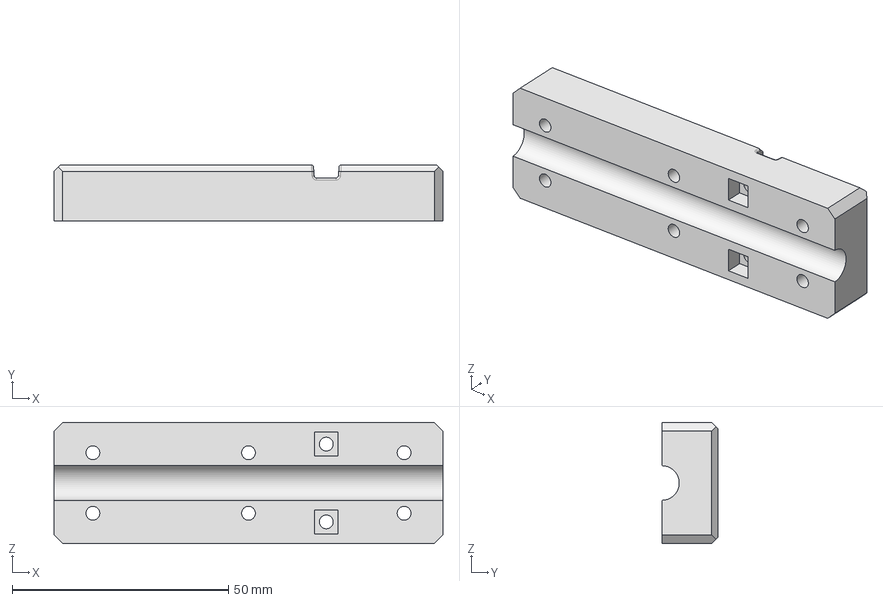
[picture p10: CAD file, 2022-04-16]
Tool/th3 axle mount.step
90.0 x 13.0 x 28.0 mm

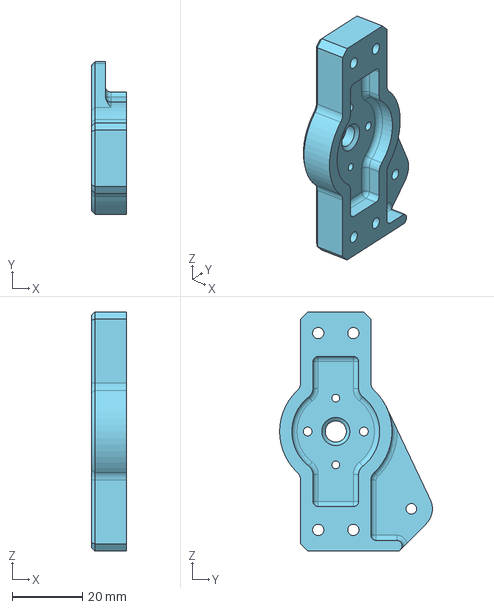
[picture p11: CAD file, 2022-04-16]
Tool/th3 motor mount.step
10.0 x 43.5 x 68.0 mm

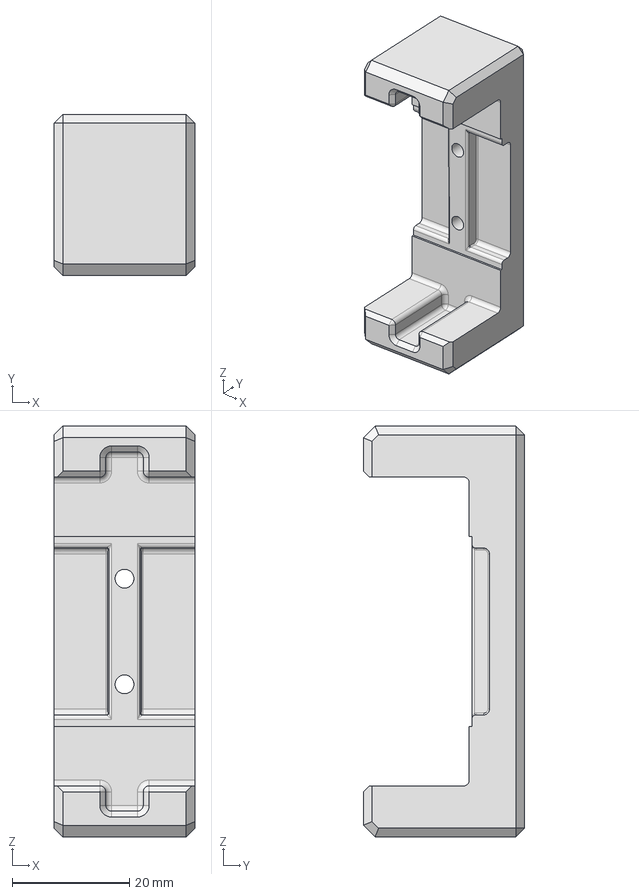
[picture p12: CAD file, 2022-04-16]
Tool/th3 lock.step
24.0 x 27.5 x 70.0 mm

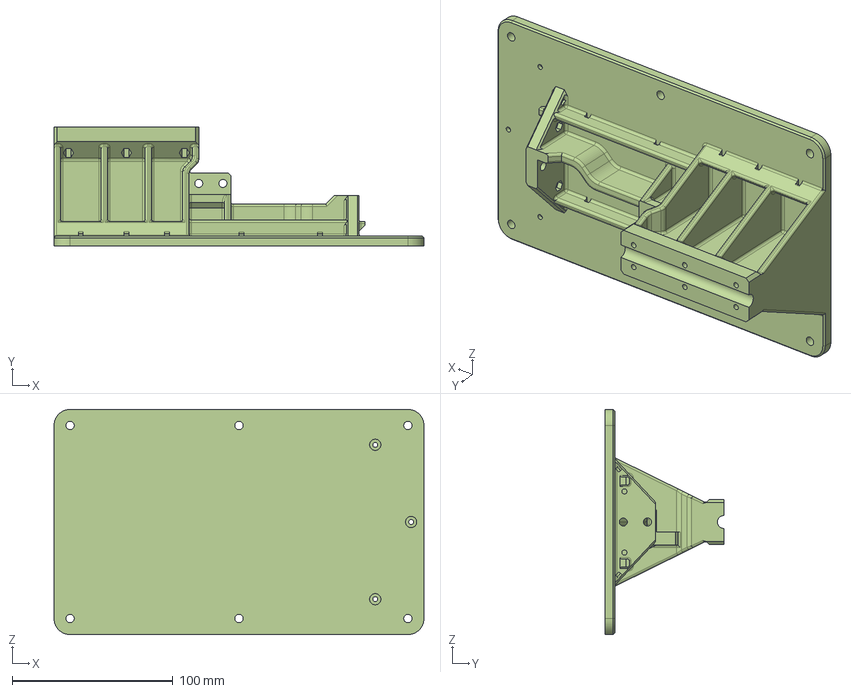
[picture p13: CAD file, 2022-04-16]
Tool/th3 stand.step
230.0 x 73.8 x 140.0 mm

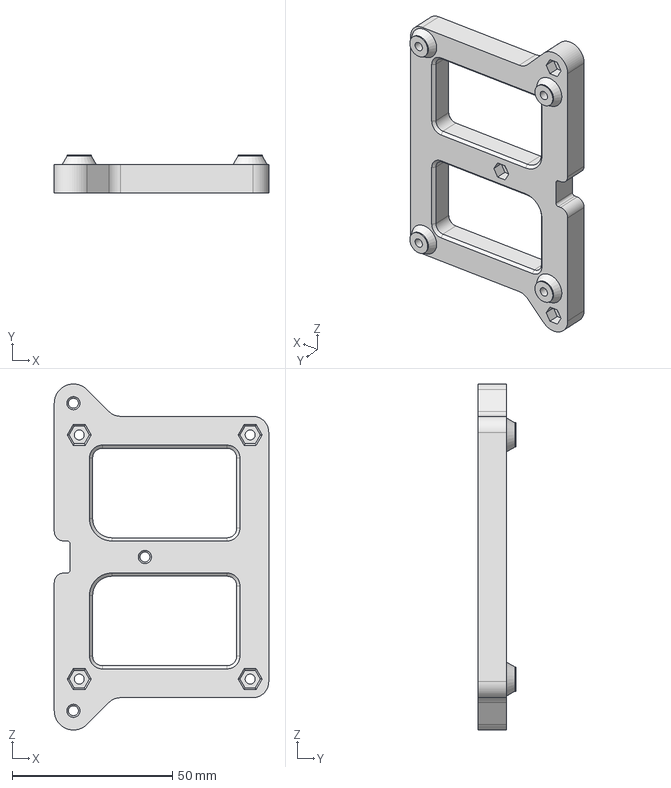
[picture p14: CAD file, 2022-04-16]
Tool/th3 board mount.step
67.0 x 12.0 x 108.0 mm

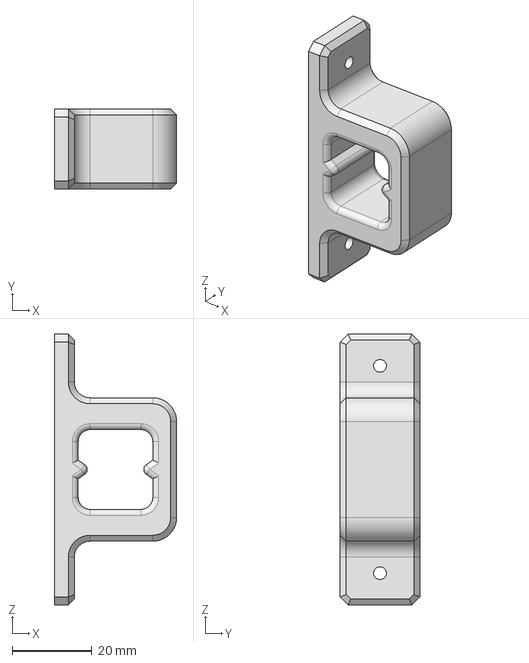
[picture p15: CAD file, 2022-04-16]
Tool/th3 thrust adapter.step
30.7 x 20.0 x 68.0 mm

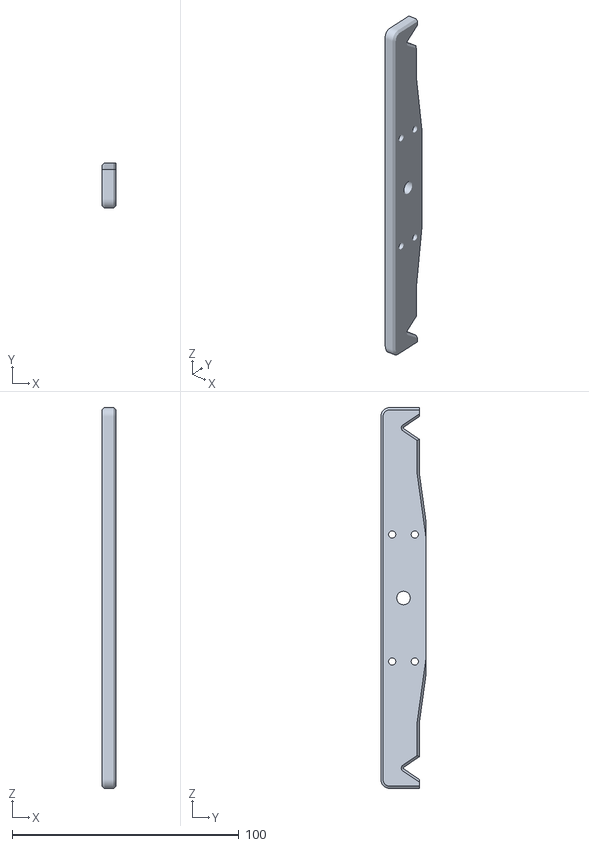
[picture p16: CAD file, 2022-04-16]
Tool/th3 torque calib arm.stl
6.00 x 20.0 x 168.0

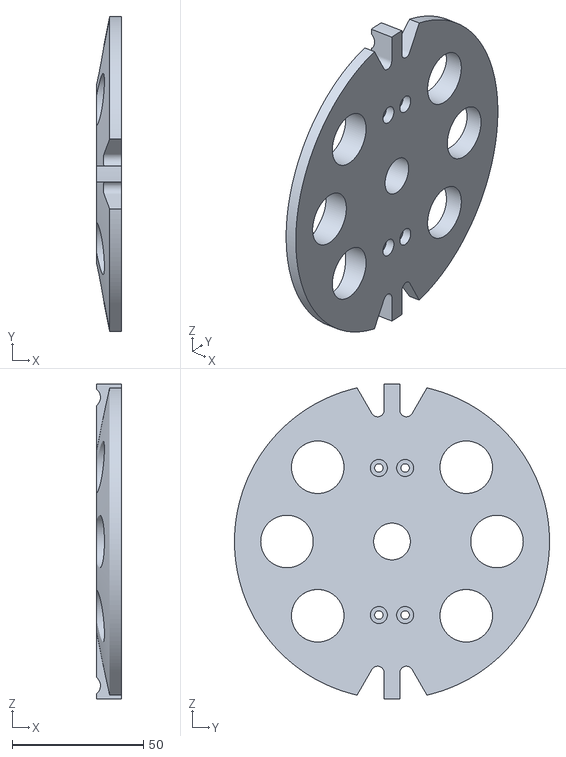
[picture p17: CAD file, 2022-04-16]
Tool/th3 thrust calib tray.stl
9.50 x 120.0 x 120.0

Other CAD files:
Tool/th3 axle mount.stl
Tool/th3 board mount.stl
Tool/th3 lock.stl
Tool/th3 motor mount.stl
Tool/th3 spindle.stl
Tool/th3 stand.stl
Tool/th3 thrust adapter.stl

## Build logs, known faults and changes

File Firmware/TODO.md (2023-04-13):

## TODO

### firmware
* process current fault on PB5
* RPM measurement fixing and testing
* Add msg_id to DATA_STREAM messages
* ChibiOS EFL driver for internal flash?
* check RTC for time stamp
* DSHOT output, DMA and PWM cycle
* ChibiOS equivalent of:
  - `HAL_TIM_OC_Start(&htim4, TIM_CHANNEL_1);`
  - `HAL_DMA_Start_IT(&hdma_tim4_ch1, (uint32_t)Wave_LUT, DestAddress, NS);`
  - `__HAL_TIM_ENABLE_DMA(&htim4, TIM_DMA_CC1);`

### hardware v2
* low-pass filter for ADC
  
## MEMO  
### sensor settings
  
* stgauge_scale_thrust	2kG -- 1054.501 1/G
* stgauge_scale_thrust	3kG -- 789.475 1/G

* stgauge_scale_torque	1kG -- 1740.526 1/G
* stgauge_scale_torque	2kG -- 1034.647 1/G

* adc_icoeff 	(ACS709)	+- 75A [0.028V/A 5V] 	-- 178.57 - 181.33 corrected (diff 1.5%) - shold be x1.042
* adc_icoeff	(ACHS-7125)	+- 50A [0.04V/A 5V] 	-- 125
* adc_icoeff	ACHS-7124)	+- 40A [0.05V/A 5V] 	-- 100
* adc_icoeff	(ACS711EX)	+- 15.5A [0.09V/A 3.3V] -- 36.7

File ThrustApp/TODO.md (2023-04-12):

## TODO

### thapp
* resend THSP_DATASTREAM_STOP in case the response is missing/timeouted

## MEMO
thrust calibration data 17.08.2021 rev.8e071b3
 - thrust coefficient = 1054.501

### calibration data 16.08.2022
 - thrust coefficient (2kG) = 1054.501
 - thrust offset = 63.300
 - torque coefficient (1kG) = 1740.526
 - torque offset = 39.200
 - torque length = 35 mm
 - vbat correction = 1.0091
 - current coefficient (70A) = 178.600
 - current raw zero (70A) = 2035
 - current coefficient (30A) = 36.700

### settings on 09.04.2023 rev.e514535
 - thrust coefficient (3kG) = 789.475
 - thrust offset = 70163
 - torque coefficient (2kG) = 1034.646
 - torque offset = 57818
 - torque length = 35 mm
 - vbat correction = 0.9918
 - current coefficient (70A; default 178.600) = 181.330
 - current raw zero (70A) = 2034
 - current coefficient (30A; default 36.700) =

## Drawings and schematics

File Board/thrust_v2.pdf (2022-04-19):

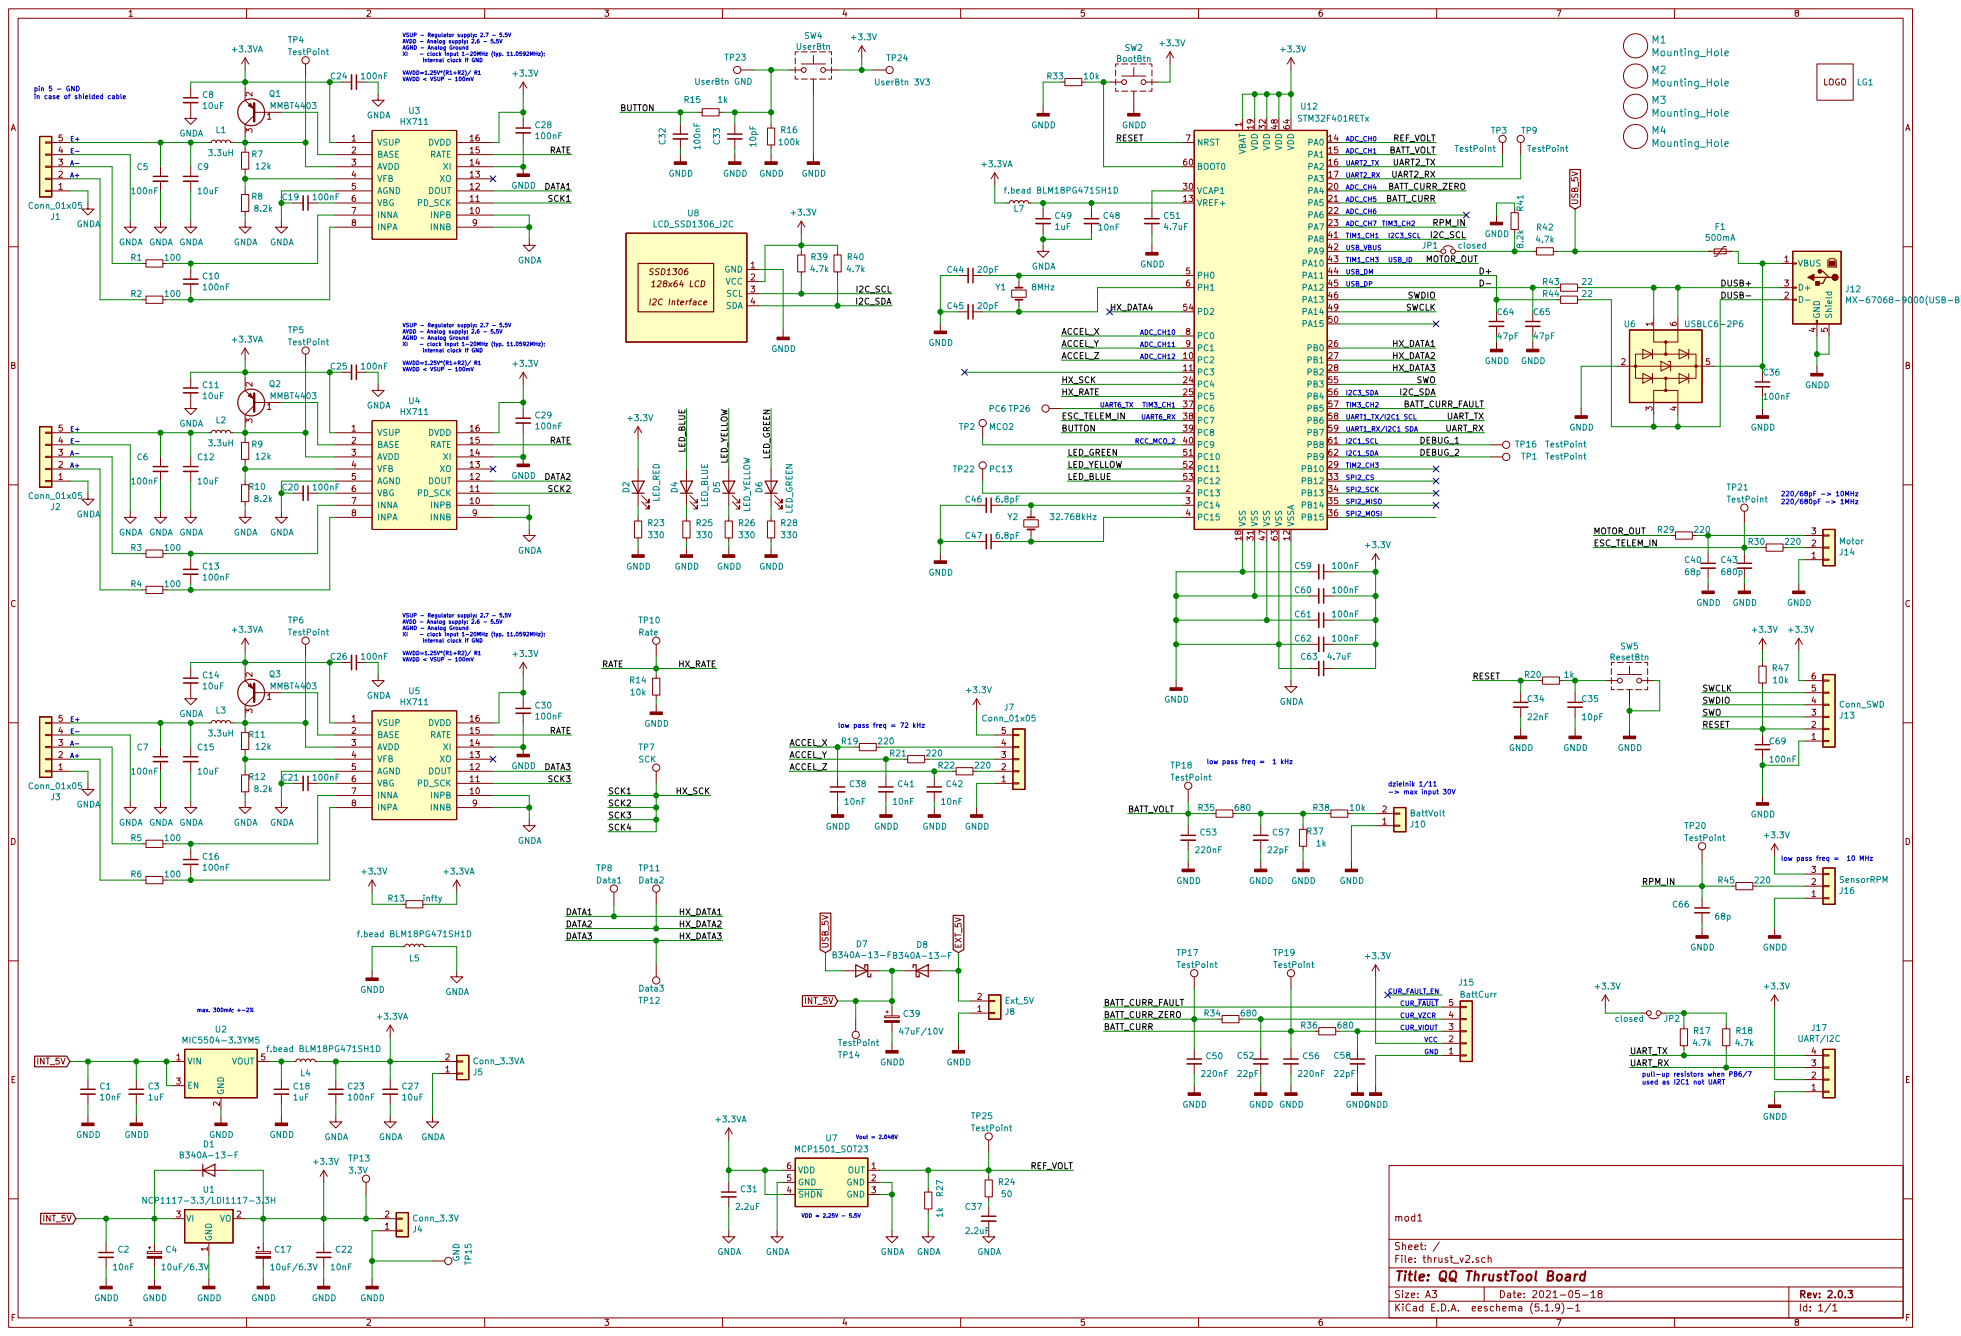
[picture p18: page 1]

VSUP - Regulator supply: 2.7 - 5.5V
AVDD - Analog supply: 2.6 - 5.5V
AGND - Analog Ground XI - clock input 1-20MHz (typ. 11.0592MHz);

internal clock if GND

1 VCAP1 30 VDD 19 VDD 32 VDD 48 VDD 64 VREF+ 13 VSS 18 VSS 31 VSS 47 VSS 63 VSSA 12 U12 STM32F401RETx C51

the SRP (weak drive). 220/68pF -> 10MHz 220/680pF -> 1MHz

low pass freq = 72 kHz

low pass freq = 1 kHz

low pass freq = 10 MHz pull-up resistors when PB6/7 used as I2C1 not UART

Id: 1/1 Title: QQ ThrustTool Board

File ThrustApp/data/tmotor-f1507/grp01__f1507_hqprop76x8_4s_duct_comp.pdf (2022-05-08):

## Tool info

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

## Measurement info

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

## Measurement Results without Duct:

Output [%] | Thrust [G] | Torque [G cm] | RPM [1/min] | Voltage [V] | Current [A] | Pin [W] | ThrustEff [G/W]
| mean std dev | mean std dev | mean std dev | mean std dev | mean std dev
20 25 30 35 40 45 50 55 60 65 70 75 80 90 100 | 30.04 0.208 47.24 0.273 66.96 0.173 85.92 0.248 106.30 0.386 125.50 0.404 144.74 2.850 181.63 0.499 211.97 1.136 243.71 0.752 278.24 0.840 309.61 2.277 339.82 3.009 410.71 2.651 460.15 3.974 | 49.06 0.202 73.99 0.350 103.19 0.222 131.30 0.202 163.26 0.409 195.91 0.415 234.91 1.405 275.72 0.804 325.09 1.014 369.21 1.334 411.30 1.363 463.93 3.978 514.46 4.794 602.54 5.925 689.96 7.139 | 8138 121.4 9842 80.8 11444 115.9 12763 243.4 14104 252.7 15512 376.6 16786 404.6 18267 291.4 19533 583.1 20708 426.4 22175 511.6 23169 449.1 24354 545.8 26446 456.2 27885 318.5 | 16.668 0.0072 16.649 0.0073 16.627 0.0081 16.601 0.0075 16.567 0.0074 16.529 0.0099 16.480 0.0082 16.427 0.0127 16.358 0.0109 16.284 0.0133 16.196 0.0127 16.097 0.0126 15.990 0.0097 15.806 0.0173 15.596 0.0183 | 0.408 0.0121 0.664 0.0181 0.988 0.0145 1.346 0.0201 1.766 0.0253 1.924 0.0267 1.971 0.0373 2.083 0.0535 2.317 0.0438 2.926 0.0548 3.798 0.0963 5.096 0.0732 6.883 0.0699 11.040 0.1127 15.245 0.1090 | 6.800 11.058 16.424 22.352 29.257 31.798 32.486 34.224 37.908 47.641 61.514 82.030 110.062 174.498 237.763 | 4.417 4.273 4.077 3.844 3.633 3.947 4.456 5.307 5.592 5.115 4.523 3.774 3.088 2.354 1.935

## Measurement Results with Duct:

Output [%] | Thrust [G] | Torque [G cm] | RPM [1/min] | Voltage [V] | Current [A] | Pin [W] | ThrustEff [G/W]
| mean std dev | mean std dev | mean std dev | mean std dev | mean std dev
20 25 30 35 40 45 50 55 60 65 70 75 80 90 100 | 36.19 0.901 54.59 0.774 78.09 0.777 101.89 0.824 121.84 0.830 148.23 0.844 177.38 0.891 209.49 0.896 248.30 1.149 286.57 1.603 323.12 1.204 360.33 1.595 398.91 1.761 485.15 3.696 551.97 6.166 | 43.11 0.289 68.57 0.268 91.36 0.381 121.68 0.569 145.77 0.749 174.95 0.907 214.64 0.795 254.91 1.193 287.80 1.215 338.44 2.536 380.84 2.177 432.03 1.998 471.44 2.419 571.83 6.384 651.32 10.546 | 8233 87.6 10014 116.3 11772 157.1 13238 188.5 14480 169.5 15979 523.5 17415 300.2 18673 435.7 20116 556.9 21542 518.3 22909 526.4 24258 720.2 25330 403.9 27755 416.2 29308 283.0 | 16.675 0.0065 16.657 0.0091 16.632 0.0084 16.608 0.0076 16.576 0.0078 16.541 0.0093 16.494 0.0112 16.435 0.0111 16.372 0.0092 16.297 0.0157 16.216 0.0113 16.121 0.0118 16.013 0.0137 15.827 0.0174 15.616 0.0170 | 0.391 0.0140 0.622 0.0186 0.932 0.0206 1.298 0.0205 1.651 0.0263 1.943 0.0254 2.052 0.0259 2.183 0.0356 2.478 0.0411 3.087 0.0412 3.863 0.0609 5.183 0.0600 6.872 0.0843 10.574 0.1176 14.701 0.1102 | 6.524 10.360 15.494 21.550 27.369 32.141 33.843 35.875 40.566 50.310 62.637 83.550 110.043 167.343 229.564 | 5.547 5.269 5.040 4.728 4.452 4.612 5.241 5.839 6.121 5.696 5.159 4.313 3.625 2.899 2.404

1

## Plots for Measurement Results:

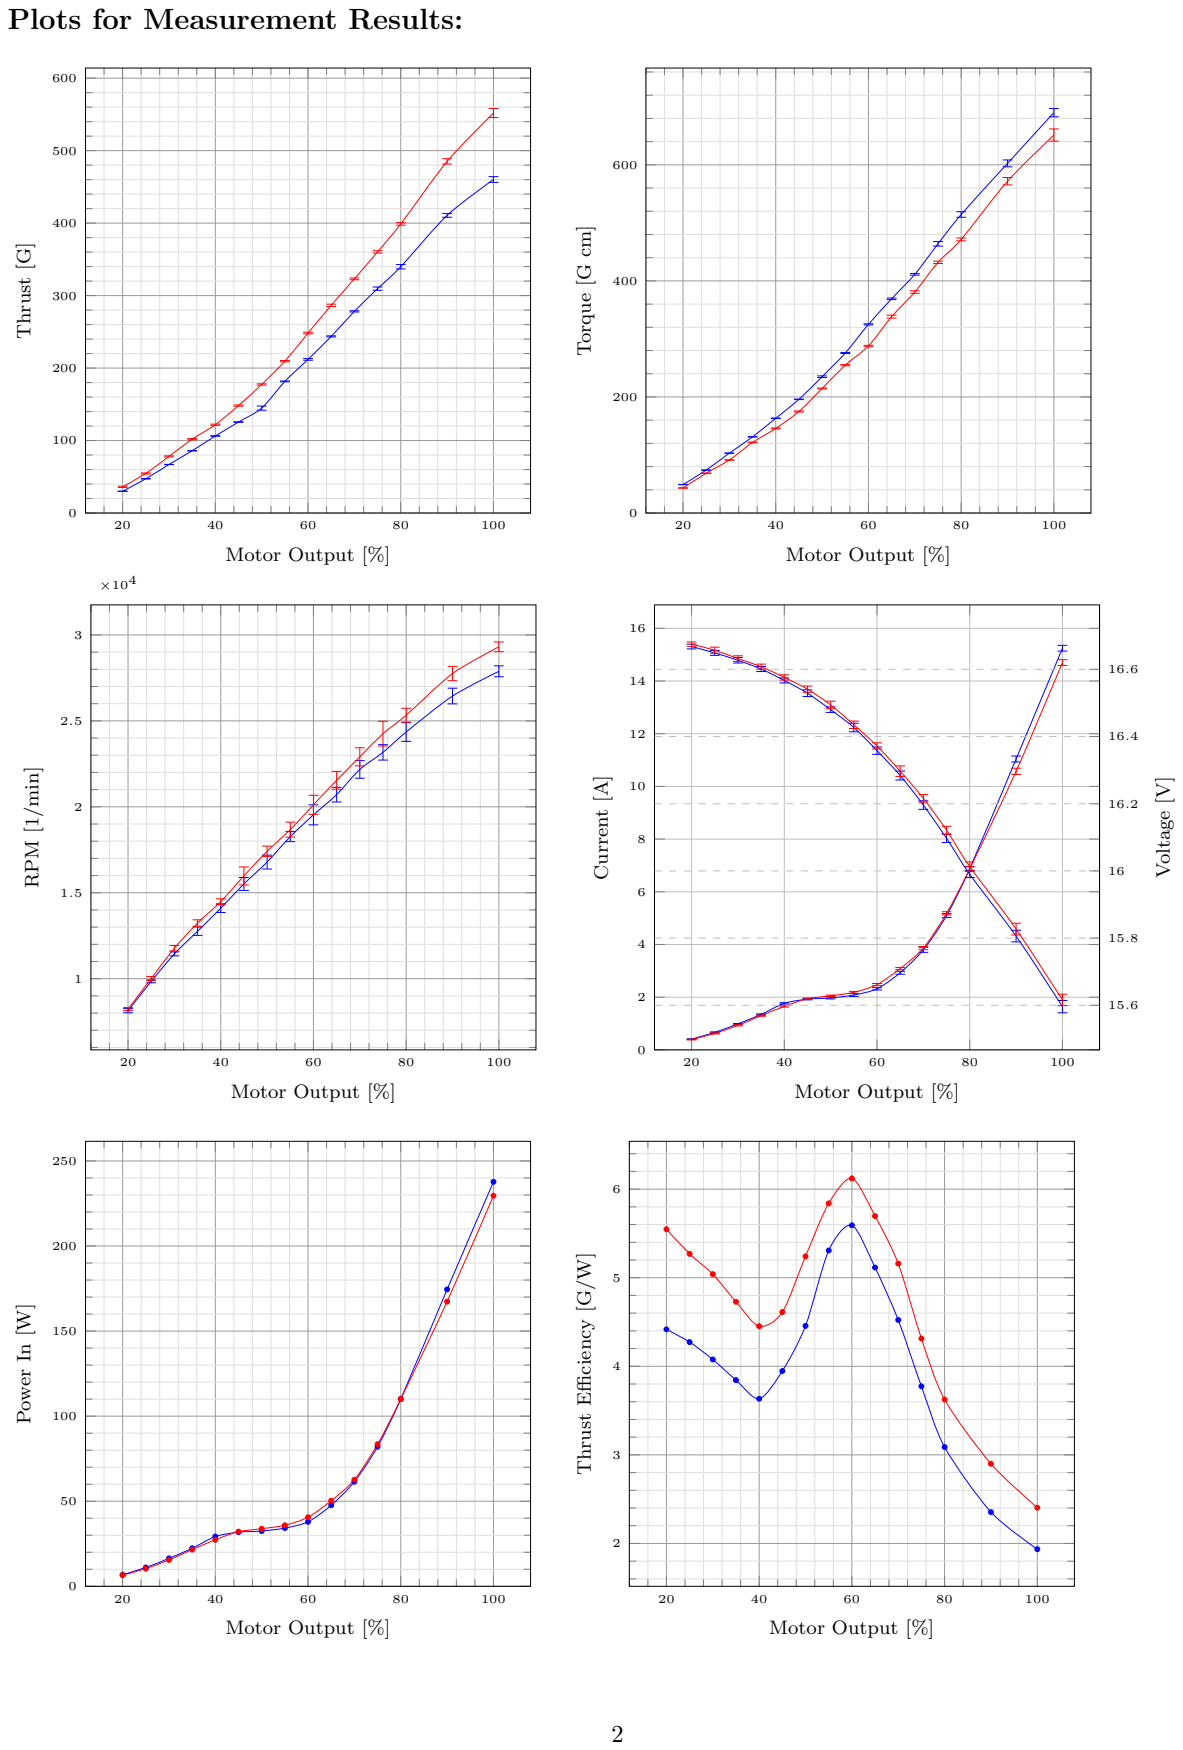
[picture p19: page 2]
Motor Output [%]; Thrust [G]; Torque [G cm]; RPM [1/min]; Current [A]; Voltage [V]; Power In [W]; Thrust Efficiency [G/W]

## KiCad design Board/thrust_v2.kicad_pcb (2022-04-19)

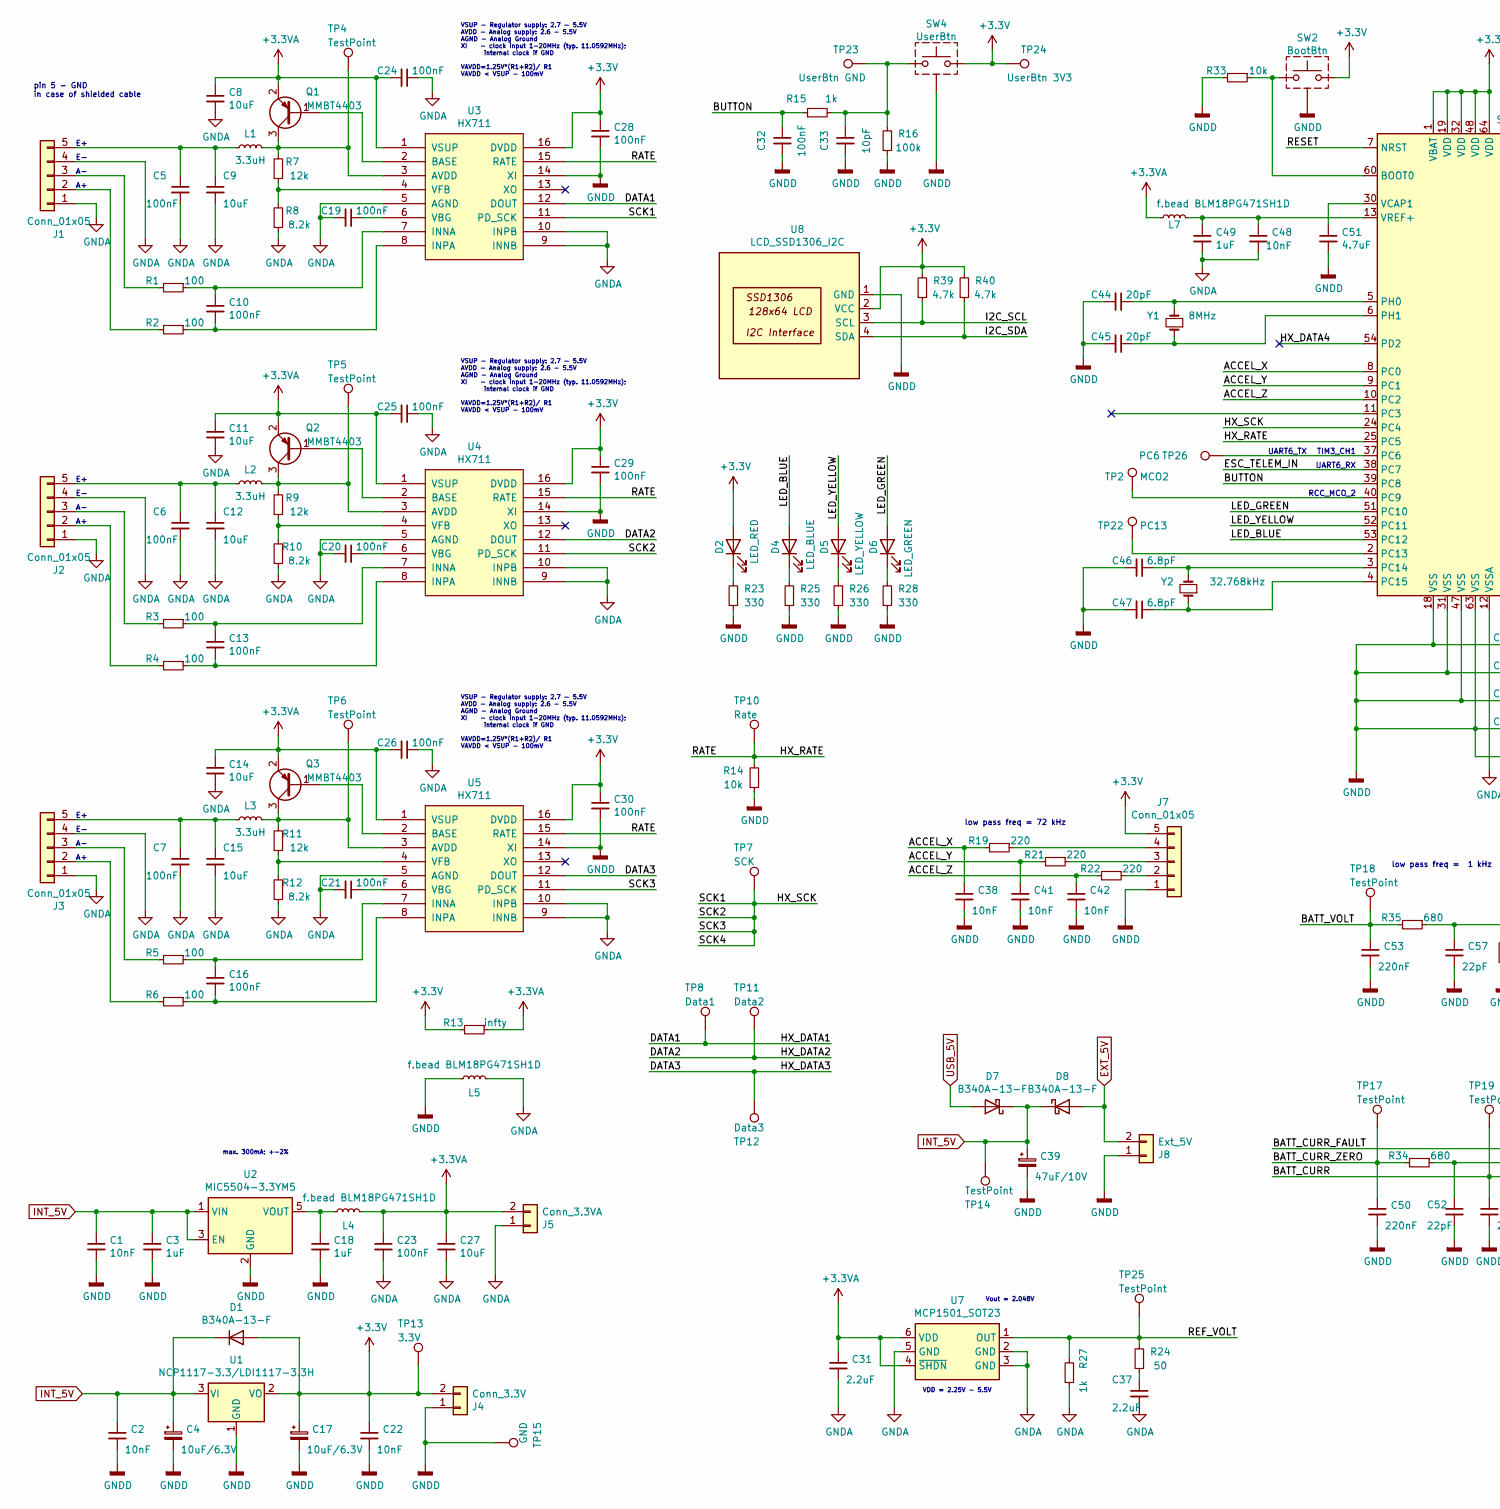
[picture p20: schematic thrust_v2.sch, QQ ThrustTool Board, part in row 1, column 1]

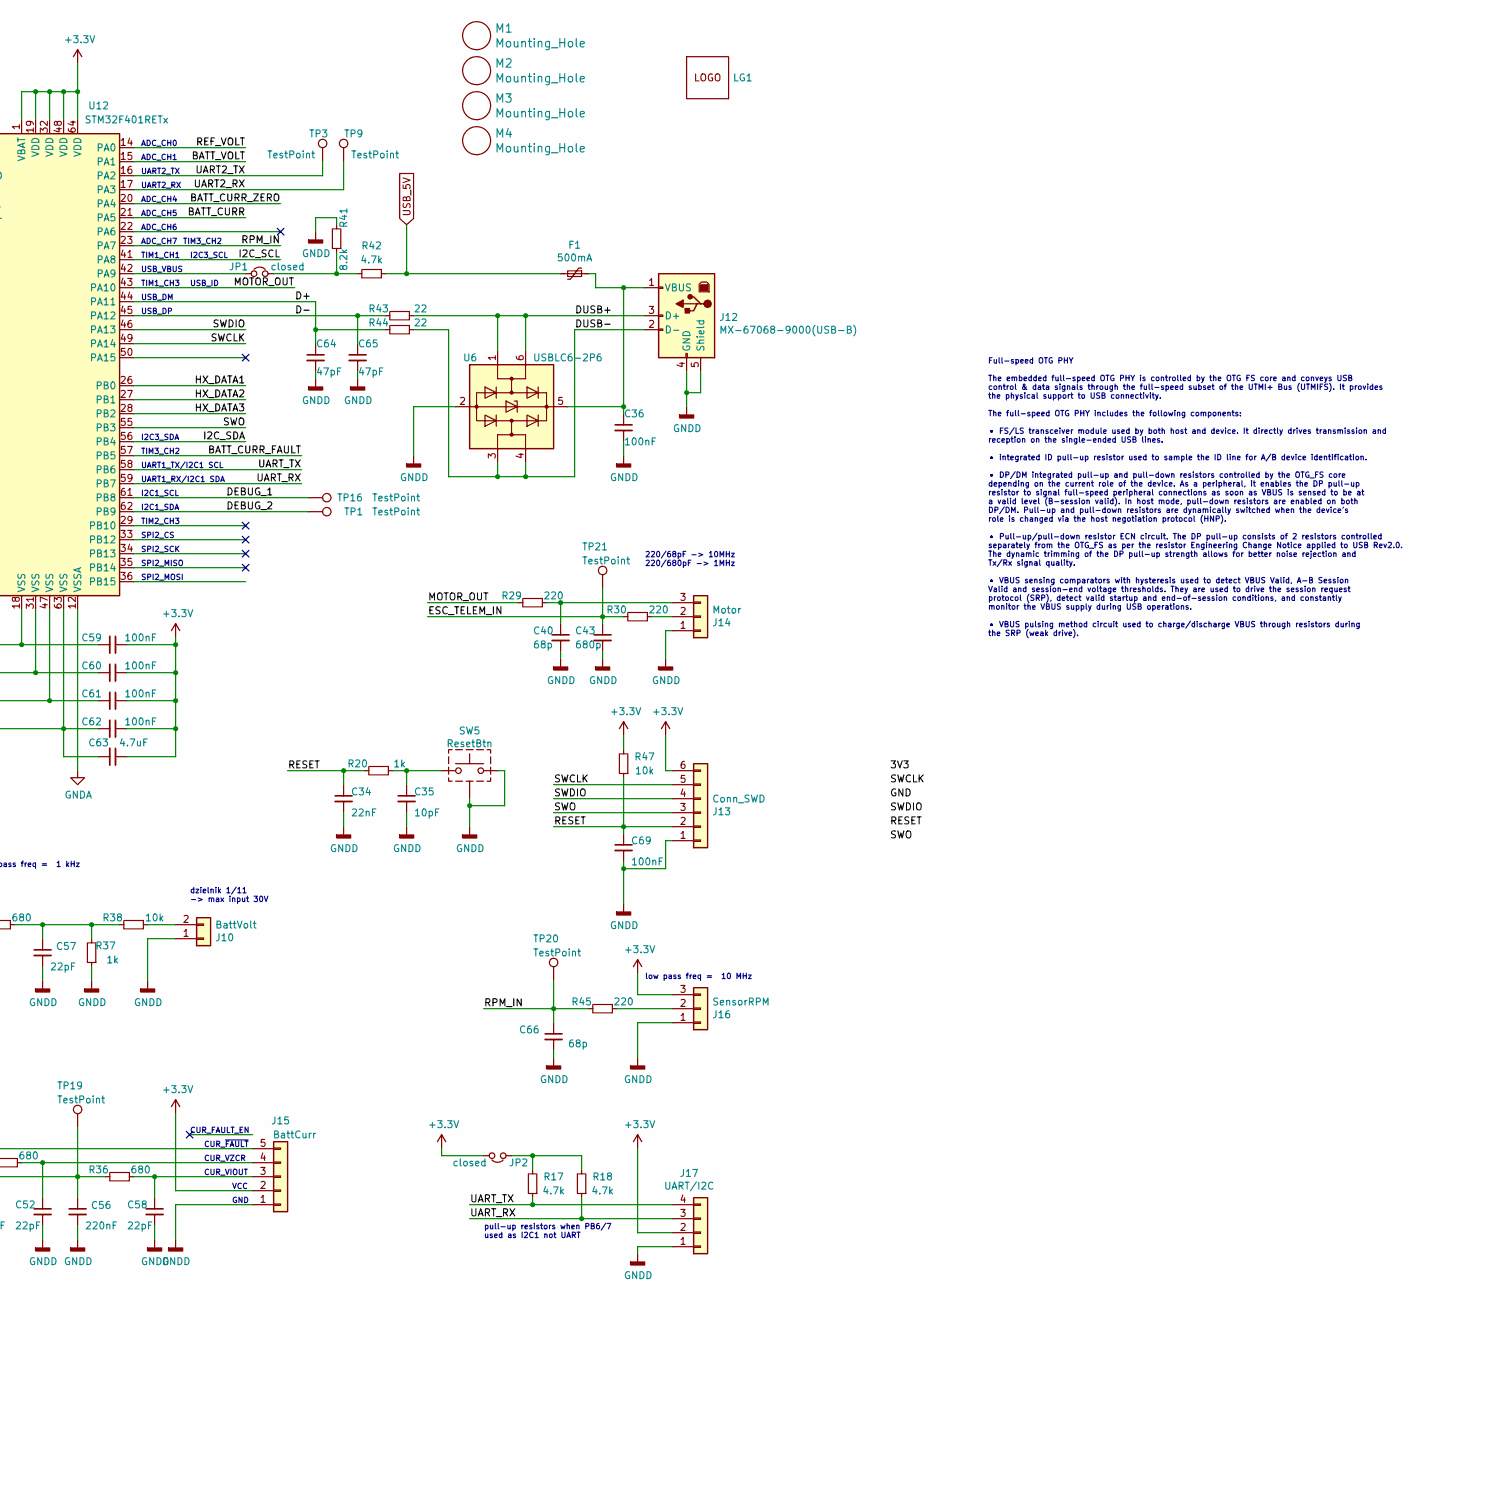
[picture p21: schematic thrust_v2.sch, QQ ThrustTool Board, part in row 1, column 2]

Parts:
C1, C2, C22, C38, C41, C42, C48: 10nF; C_0603_1608Metric_Pad1.08x0.95mm_HandSolder
C3, C18, C49: 1uF; C_0603_1608Metric_Pad1.08x0.95mm_HandSolder
C4, C17: 10uF/6.3V; CP_EIA-3528-21_Kemet-B_Pad1.50x2.35mm_HandSolder
C5, C6, C7, C10, C13, C16, C19, C20, C21, C23, C24, C25, C26, C28, C29, C30, C32, C36, C59, C60, C61, C62, C69: 100nF; C_0603_1608Metric_Pad1.08x0.95mm_HandSolder
C8, C9, C11, C12, C14, C15, C27: 10uF; C_0603_1608Metric_Pad1.08x0.95mm_HandSolder
C31, C37: 2.2uF; C_0603_1608Metric_Pad1.08x0.95mm_HandSolder
C33, C35: 10pF; C_0603_1608Metric_Pad1.08x0.95mm_HandSolder
C34: 22nF; C_0603_1608Metric_Pad1.08x0.95mm_HandSolder
C39: 47uF/10V; CP_EIA-3528-21_Kemet-B_Pad1.50x2.35mm_HandSolder
C40, C66: 68p; C_0603_1608Metric_Pad1.08x0.95mm_HandSolder
C43: 680p; C_0603_1608Metric_Pad1.08x0.95mm_HandSolder
C44, C45: 20pF; C_0603_1608Metric_Pad1.08x0.95mm_HandSolder
C46, C47: 6.8pF; C_0603_1608Metric_Pad1.08x0.95mm_HandSolder
C50, C53, C56: 220nF; C_0603_1608Metric_Pad1.08x0.95mm_HandSolder
C51, C63: 4.7uF; C_0603_1608Metric_Pad1.08x0.95mm_HandSolder
C52, C57, C58: 22pF; C_0603_1608Metric_Pad1.08x0.95mm_HandSolder
C64, C65: 47pF; C_0603_1608Metric_Pad1.08x0.95mm_HandSolder
D1, D7, D8: B340A-13-F; D_SMA
D2: LED_RED; LED_0603_1608Metric_Pad1.05x0.95mm_HandSolder
D4: LED_BLUE; LED_0603_1608Metric_Pad1.05x0.95mm_HandSolder
D5: LED_YELLOW; LED_0603_1608Metric_Pad1.05x0.95mm_HandSolder
D6: LED_GREEN; LED_0603_1608Metric_Pad1.05x0.95mm_HandSolder
F1: 500mA; Fuse_0805_2012Metric_Pad1.15x1.40mm_HandSolder
J1, J2, J3, J7: Conn_01x05; PinHeader_1x05_P2.54mm_Vertical
J4: Conn_3.3V; PinHeader_1x02_P2.54mm_Vertical
J5: Conn_3.3VA; PinHeader_1x02_P2.54mm_Vertical
J8: Ext_5V; PinHeader_1x02_P2.54mm_Vertical
J10: BattVolt; PinHeader_1x02_P2.54mm_Vertical
J12: MX-67068-9000(USB-B); USB_B_OST_USB-B1HSxx_Horizontal_mod
J13: Conn_SWD; PinHeader_1x06_P2.54mm_Vertical
J14: Motor; PinHeader_1x03_P2.54mm_Vertical
J15: BattCurr; PinHeader_1x05_P2.54mm_Vertical
J16: SensorRPM; PinHeader_1x03_P2.54mm_Vertical
J17: UART/I2C; PinHeader_1x04_P2.54mm_Vertical
JP1, JP2: closed; SolderJumper-2_P1.3mm_Open_TrianglePad1.0x1.5mm
L1, L2, L3: 3.3uH; L_0603_1608Metric_Pad1.05x0.95mm_HandSolder
L4, L5, L7: f.bead BLM18PG471SH1D; L_0603_1608Metric_Pad1.05x0.95mm_HandSolder
LG1: Logo_1; LOGO_QX4_knot_circ2_24mm
M1, M2, M3, M4: Mounting_Hole; MountingHole_3.2mm_M3
Q1, Q2, Q3: MMBT4403; SOT-23
R1, R2, R3, R4, R5, R6: 100; R_0603_1608Metric_Pad0.98x0.95mm_HandSolder
R7, R9, R11: 12k; R_0603_1608Metric_Pad0.98x0.95mm_HandSolder
R8, R10, R12, R41: 8.2k; R_0603_1608Metric_Pad0.98x0.95mm_HandSolder
R13: infty; R_0603_1608Metric_Pad0.98x0.95mm_HandSolder
R14, R33, R38, R47: 10k; R_0603_1608Metric_Pad0.98x0.95mm_HandSolder
R15, R20, R27, R37: 1k; R_0603_1608Metric_Pad0.98x0.95mm_HandSolder
R16: 100k; R_0603_1608Metric_Pad0.98x0.95mm_HandSolder
R17, R18, R39, R40, R42: 4.7k; R_0603_1608Metric_Pad0.98x0.95mm_HandSolder
R19, R21, R22, R29, R30, R45: 220; R_0603_1608Metric_Pad0.98x0.95mm_HandSolder
R23, R25, R26, R28: 330; R_0603_1608Metric_Pad0.98x0.95mm_HandSolder
R24: 50; R_0603_1608Metric_Pad0.98x0.95mm_HandSolder
R34, R35, R36: 680; R_0603_1608Metric_Pad0.98x0.95mm_HandSolder
R43, R44: 22; R_0603_1608Metric_Pad0.98x0.95mm_HandSolder
SW2: BootBtn; SW_Push_1P1T-SH_NO_CK_KMR2xxG
SW4: UserBtn; SW_SPST_Panasonic_EVQPL_3PL_5PL_PT_A15
SW5: ResetBtn; SW_Push_1P1T-SH_NO_CK_KMR2xxG
TP1, TP3, TP9, TP14, TP16, TP17, TP18, TP19, TP20, TP21: TestPoint; TestPoint_Pad_1.5x1.5mm
TP2: MCO2; TestPoint_Pad_1.5x1.5mm
TP4, TP5, TP6, TP25: TestPoint; TestPoint_Pad_D1.0mm
TP7: SCK; TestPoint_Pad_1.5x1.5mm
TP8: Data1; TestPoint_Pad_1.5x1.5mm
TP10: Rate; TestPoint_Pad_1.5x1.5mm
TP11: Data2; TestPoint_Pad_1.5x1.5mm
TP12: Data3; TestPoint_Pad_1.5x1.5mm
TP13: 3.3V; TestPoint_Pad_1.5x1.5mm
TP15: GND; TestPoint_Pad_1.5x1.5mm
TP22: PC13; TestPoint_Pad_1.5x1.5mm
TP23: UserBtn GND; TestPoint_Pad_1.5x1.5mm
TP24: UserBtn 3V3; TestPoint_Pad_1.5x1.5mm
TP26: PC6; TestPoint_Pad_1.5x1.5mm
U1: NCP1117-3.3/LDI1117-3.3H; SOT-223-3_TabPin2
U2: MIC5504-3.3YM5; SOT-23-5
U3, U4, U5: HX711; SOIC-16_3.9x9.9mm_P1.27mm
U6: USBLC6-2P6; SOT-23-6
U7: MCP1501_SOT23; SOT-23-6
U8: LCD_SSD1306_I2C; PinHeader_1x04_P2.54mm_Vertical
U12: STM32F401RETx; LQFP-64_10x10mm_P0.5mm
Y1: 8MHz; Crystal_HC49-4H_Vertical
Y2: 32.768kHz; ABS25

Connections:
+3.3VA: C8.1, C11.1, C14.1, C23.1, C24.2, C25.2, C26.2, C27.1, C31.1, J5.2, L4.2, L7.1, Q1.2 (E), Q2.2 (E), Q3.2 (E), R13.1, U3.1 (VSUP), U4.1 (VSUP), U5.1 (VSUP), U7.4 (~SHDN), U7.6 (VDD)
+3V3: C17.1, C22.1, C28.1, C29.1, C30.1, C59.1, C60.1, C61.1, C62.1, C63.1, D1.2 (A), D2.2 (A), J4.2, J7.5, J13.6, J15.2, J16.3, J17.2, JP2.2, R13.2, R39.2, R40.2, R47.2, SW2.2, SW4.2, TP13.1, TP24.1, U1.2 (VO), U3.16 (DVDD), U4.16 (DVDD), U5.16 (DVDD), U8.2 (VCC), U12.1 (VBAT), U12.19 (VDD), U12.32 (VDD), U12.48 (VDD), U12.64 (VDD)
/ACCEL_X: C38.1, R19.2, U12.8 (PC0)
/ACCEL_Y: C41.1, R21.2, U12.9 (PC1)
/ACCEL_Z: C42.1, R22.2, U12.10 (PC2)
/BATT_CURR: C56.1, R36.2, TP19.1, U12.21 (PA5)
/BATT_CURR_FAULT: J15.5, U12.57 (PB5)
/BATT_CURR_ZERO: C50.1, R34.2, TP17.1, U12.20 (PA4)
/BATT_VOLT: C53.1, R35.2, TP18.1, U12.15 (PA1)
/BUTTON: C32.1, R15.1, U12.39 (PC8)
/D+: C64.1, R44.2, U12.44 (PA11)
/D-: C65.1, R43.2, U12.45 (PA12)
/DATA1: TP8.1, U3.12 (DOUT), U12.26 (PB0)
/DATA2: TP11.1, U4.12 (DOUT), U12.27 (PB1)
/DATA3: TP12.1, U5.12 (DOUT), U12.28 (PB2)
/DEBUG_1: TP16.1, U12.61 (PB8)
/DEBUG_2: TP1.1, U12.62 (PB9)
/DUSB+: J12.3 (D+), R43.1, U6.1 (I/O1), U6.6 (I/O1)
/DUSB-: J12.2 (D-), R44.1, U6.3 (I/O2), U6.4 (I/O2)
/ESC_TELEM_IN: C43.1, R30.2, TP21.1, U12.38 (PC7)
/HX_DATA4: U12.54 (PD2)
/HX_RATE: R14.2, TP10.1, U3.15 (RATE), U4.15 (RATE), U5.15 (RATE), U12.25 (PC5)
/HX_SCK: TP7.1, U3.11 (PD_SCK), U4.11 (PD_SCK), U5.11 (PD_SCK), U12.24 (PC4)
/I2C_SCL: R39.1, U8.3 (SCL), U12.41 (PA8)
/I2C_SDA: R40.1, U8.4 (SDA), U12.56 (PB4)
/LED_BLUE: D4.2 (A), U12.53 (PC12)
/LED_GREEN: D6.2 (A), U12.51 (PC10)
/LED_YELLOW: D5.2 (A), U12.52 (PC11)
/MOTOR_OUT: R29.2, U12.43 (PA10)
/REF_VOLT: R24.2, R27.2, TP25.1, U7.1 (OUT), U12.14 (PA0)
/RESET: C34.1, C69.1, J13.2, R20.2, R47.1, U12.7 (NRST)
/RPM_IN: C66.1, R45.2, TP20.1, U12.23 (PA7)
/SWCLK: J13.5, U12.49 (PA14)
/SWDIO: J13.4, U12.46 (PA13)
/SWO: J13.3, U12.55 (PB3)
/UART2_RX: TP9.1, U12.17 (PA3)
/UART2_TX: TP3.1, U12.16 (PA2)
/UART_RX: J17.3, R18.1, U12.59 (PB7)
/UART_TX: J17.4, R17.1, U12.58 (PB6)
EXT_5V: D8.2 (A), J8.2
GNDA: C5.2, C6.2, C7.2, C8.2, C9.2, C11.2, C12.2, C14.2, C15.2, C19.2, C20.2, C21.2, C23.2, C24.1, C25.1, C26.1, C27.2, C31.2, C37.2, C48.2, C49.2, J1.1, J1.4, J2.1, J2.4, J3.1, J3.4, J5.1, L5.2, R8.1, R10.1, R12.1, R27.1, U3.5 (AGND), U3.9 (INNB), U3.10 (INPB), U4.5 (AGND), U4.9 (INNB), U4.10 (INPB), U5.5 (AGND), U5.9 (INNB), U5.10 (INPB), U7.2 (GND), U7.3 (GND), U7.5 (GND), U12.12 (VSSA)
GNDD: C1.2, C2.2, C3.2, C4.2, C17.2, C18.2, C22.2, C28.2, C29.2, C30.2, C32.2, C33.2, C34.2, C35.2, C36.2, C38.2, C39.2, C40.2, C41.2, C42.2, C43.2, C44.2, C45.2, C46.2, C47.2, C50.2, C51.2, C52.2, C53.2, C56.2, C57.2, C58.2, C59.2, C60.2, C61.2, C62.2, C63.2, C64.2, C65.2, C66.2, C69.2, J4.1, J7.1, J8.1, J10.1, J12.4 (GND), J12.5 (Shield), J13.1, J14.1, J15.1, J16.1, J17.1, L5.1, R14.1, R16.1, R23.1, R25.1, R26.1, R28.1, R33.2, R37.1, R41.2, SW2.SH (GND), SW4.0 (GND), SW5.2, SW5.SH (GND), TP15.1, U1.1 (GND), U2.2 (GND), U3.14 (XI), U4.14 (XI), U5.14 (XI), U6.2 (GND), U8.1 (GND), U12.18 (VSS), U12.31 (VSS), U12.47 (VSS), U12.63 (VSS)
INT_5V: C1.1, C2.1, C3.1, C4.1, C39.1, D1.1 (K), D7.1 (K), D8.1 (K), TP14.1, U1.3 (VI), U2.1 (VIN), U2.3 (EN)
unnamed: C5.1, C9.1, J1.5, L1.1
unnamed: C10.1, R1.1, U3.7 (INNA)
unnamed: C10.2, R2.1, U3.8 (INPA)
unnamed: C6.1, C12.1, J2.5, L2.1
unnamed: C13.1, R3.1, U4.7 (INNA)
unnamed: C13.2, R4.1, U4.8 (INPA)
unnamed: C7.1, C15.1, J3.5, L3.1
unnamed: C16.1, R5.1, U5.7 (INNA)
unnamed: C16.2, R6.1, U5.8 (INPA)
unnamed: C18.1, L4.1, U2.5 (VOUT)
unnamed: C19.1, U3.6 (VBG)
unnamed: C20.1, U4.6 (VBG)
unnamed: C21.1, U5.6 (VBG)
unnamed: C33.1, R15.2, R16.2, SW4.1, TP23.1
unnamed: C35.1, R20.1, SW5.1
unnamed: C36.1, F1.1, J12.1 (VBUS), U6.5 (VBUS)
unnamed: C37.1, R24.1
unnamed: C40.1, J14.3, R29.1
unnamed: C44.1, U12.5 (PH0), Y1.2
unnamed: C45.1, U12.6 (PH1), Y1.1
unnamed: C46.1, U12.3 (PC14), Y2.2
unnamed: C47.1, U12.4 (PC15), Y2.1
unnamed: C48.1, C49.1, L7.2, U12.13 (VREF+)
unnamed: C51.1, U12.30 (VCAP1)
unnamed: C52.1, J15.4, R34.1
unnamed: C57.1, R35.1, R37.2, R38.2
unnamed: C58.1, J15.3, R36.1
unnamed: D2.1 (K), R23.2
unnamed: D4.1 (K), R25.2
unnamed: D5.1 (K), R26.2
unnamed: D6.1 (K), R28.2
unnamed: J1.2, R2.2
unnamed: J1.3, R1.2
unnamed: J2.2, R4.2
unnamed: J2.3, R3.2
unnamed: J3.2, R6.2
unnamed: J3.3, R5.2
unnamed: J7.2, R22.1
unnamed: J7.3, R21.1
unnamed: J7.4, R19.1
unnamed: J10.2, R38.1
unnamed: J14.2, R30.1
unnamed: J16.2, R45.1
unnamed: JP1.1, U12.42 (PA9)
unnamed: JP1.2, R41.1, R42.2
unnamed: JP2.1, R17.2, R18.2
unnamed: L1.2, Q1.3 (C), R7.2, TP4.1, U3.3 (AVDD)
unnamed: L2.2, Q2.3 (C), R9.2, TP5.1, U4.3 (AVDD)
unnamed: L3.2, Q3.3 (C), R11.2, TP6.1, U5.3 (AVDD)
unnamed: Q1.1 (B), U3.2 (BASE)
unnamed: Q2.1 (B), U4.2 (BASE)
unnamed: Q3.1 (B), U5.2 (BASE)
unnamed: R7.1, R8.2, U3.4 (VFB)
unnamed: R9.1, R10.2, U4.4 (VFB)
unnamed: R11.1, R12.2, U5.4 (VFB)
unnamed: R33.1, SW2.1, U12.60 (BOOT0)
unnamed: TP2.1, U12.40 (PC9)
unnamed: TP22.1, U12.2 (PC13)
unnamed: TP26.1, U12.37 (PC6)
USB_5V: D7.2 (A), F1.2, R42.1

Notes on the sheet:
Vout = 2.048V
VDD = 2.25V - 5.5V
max. 300mA; +-2%
VSUP - Regulator supply: 2.7 - 5.5V AVDD - Analog supply: 2.6 - 5.5V AGND - Analog Ground XI - clock input 1-20MHz (typ. 11.0592MHz); internal clock if GND VAVDD=1.25V*(R1+R2)/ R1 VAVDD < VSUP - 100mV
dzielnik 1/11 -> max input 30V
CUR_FAULT_EN
CUR_~FAULT
CUR_VZCR
CUR_VIOUT
VCC
GND
pin 5 - GND in case of shielded cable
I2C3_SDA
I2C3_SCL
TIM1_CH3
SPI2_MOSI
SPI2_MISO
SPI2_SCK
RCC_MCO_2
ADC_CH5
UART2_RX
UART2_TX
TIM3_CH1
UART6_RX
TIM1_CH1
ADC_CH7
ADC_CH6
ADC_CH4
ADC_CH1
ADC_CH0
I2C1_SDA
I2C1_SCL
USB_ID
UART1_TX/I2C1 SCL
UART1_RX/I2C1 SDA
USB_VBUS
USB_DM
USB_DP
pull-up resistors when PB6/7 used as I2C1 not UART
Full-speed OTG PHY The embedded full-speed OTG PHY is controlled by the OTG FS core and conveys USB control & data signals through the full-speed subset of the UTMI+ Bus (UTMIFS). It provides the physical support to USB connectivity. The full-speed OTG PHY includes the following components: • FS/LS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

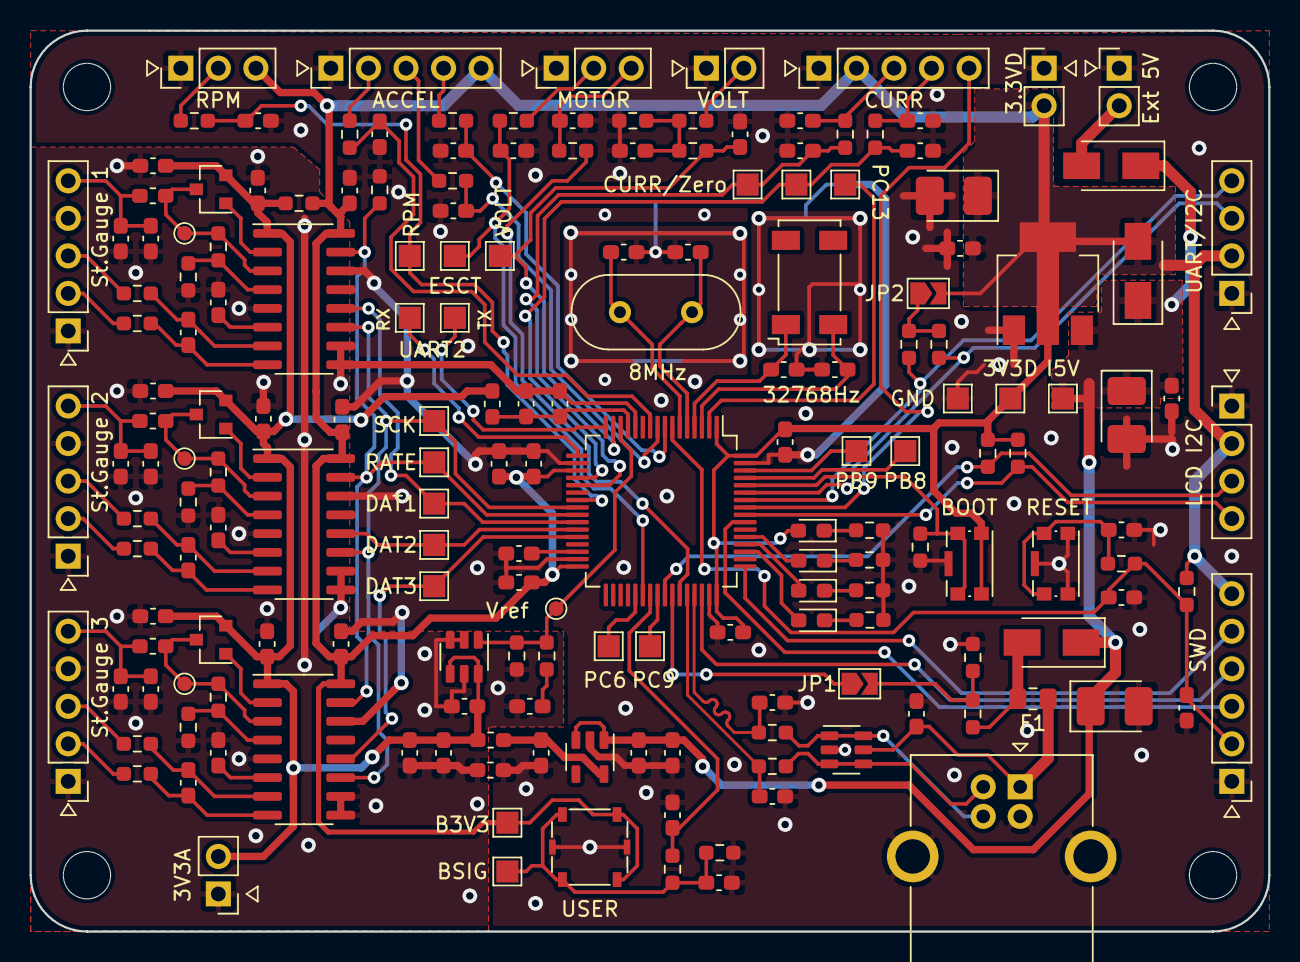
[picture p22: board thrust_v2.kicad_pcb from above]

Board: 2 copper layers, 83.8 x 61.0 mm, 187 parts (1 on the bottom side), 102 nets.

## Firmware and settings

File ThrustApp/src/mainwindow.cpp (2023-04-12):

#include <QtWidgets>

#include <QSplitter>
#include <QListView>
#include <QTreeView>
#include <QTextEdit>
#include <QLayout>
#include <QPushButton>
#include <QDebug>

#include "mainwindow.h"
#include "dlg_settings.h"





////////////////////////////////////////////////////////////////////////////////////////////////////
// class MainWindow
////////////////////////////////////////////////////////////////////////////////////////////////////
MainWindow::MainWindow(QWidget *parent)
    : QMainWindow(parent), mthSerial(nullptr), mAutoControl(this), mHBeatTimer(nullptr), mbHBeat(false)
{
    this->setStyleSheet(R"( QMainWindow::separator { background-color: rgb(215, 215, 215); } )" );

    mSerialStat = ESerialStatus::Closed;


//===========================================================
// actions 

    //const QIcon newIcon = QIcon::fromTheme("document-new", QIcon(":/images/new.png"));
    //QAction *newAct = new QAction(newIcon, tr("&New"), this);

    QAction* newAct = new QAction(tr("&New"), this);
    newAct->setShortcuts(QKeySequence::New);
    newAct->setStatusTip(tr("Create a new file"));
    connect(newAct, &QAction::triggered, this, &MainWindow::newFile);

    QAction* openAct = new QAction(tr("&Open..."), this);
    openAct->setShortcuts(QKeySequence::Open);
    openAct->setStatusTip(tr("Open an existing file"));
    connect(openAct, &QAction::triggered, this, &MainWindow::open);

    QAction* saveAct = new QAction(tr("&Save"), this);
    saveAct->setShortcuts(QKeySequence::Save);
    saveAct->setStatusTip(tr("Save the document to disk"));
    connect(saveAct, &QAction::triggered, this, &MainWindow::save);


    QAction* selTmplAct = new QAction(tr("Select Latex Template"), this);
    //exportAct->setShortcuts(QKeySequence::Save);
    selTmplAct->setStatusTip(tr("Select template for Latex report"));
    connect(selTmplAct, &QAction::triggered, this, &MainWindow::select_export_tmpl);

    QAction* exportAct = new QAction(tr("&Export"), this);
    //exportAct->setShortcuts(QKeySequence::Save);
    exportAct->setStatusTip(tr("Export the measurement report to disk"));
    connect(exportAct, &QAction::triggered, this, &MainWindow::export_rep);

    QAction* exitAct = new QAction(tr("E&xit"), this);
    exitAct->setShortcuts(QKeySequence::Quit);
    exitAct->setStatusTip(tr("Exit the application"));
    connect(exitAct, &QAction::triggered, this, &QWidget::close);

    QAction* aboutAct = new QAction(tr("&About"), this);
    aboutAct->setStatusTip(tr("Show the application's About box"));
    connect(aboutAct, &QAction::triggered, this, &MainWindow::about);

    QAction* settingsAct = new QAction(tr("&Settings"), this);
    settingsAct->setStatusTip(tr("Show the Settings Dialog"));
    connect(settingsAct, &QAction::triggered, this, &MainWindow::settings);

    // create menu 
    QMenu* fileMenu = menuBar()->addMenu(tr("&File"));
    fileMenu->addAction(newAct);
    fileMenu->addAction(openAct);
    fileMenu->addAction(saveAct);
    fileMenu->addSeparator();
    fileMenu->addAction(selTmplAct);
    fileMenu->addAction(exportAct);
    fileMenu->addSeparator();
    fileMenu->addAction(exitAct);

    QMenu* helpMenu = menuBar()->addMenu(tr("&Help"));
    helpMenu->addAction(aboutAct);

    // tool bar
    QToolBar *fileToolBar = addToolBar(tr("File"));
    fileToolBar->addAction(newAct);
    fileToolBar->addAction(openAct);
    fileToolBar->addAction(saveAct);
    fileToolBar->addAction(settingsAct);

//===========================================================
// status bar

	//statusBar()->addPermanentWidget( new QPushButton("push") );
    statusBar()->showMessage(tr("Ready"));

    labVBatCell = new QLabel(tr("-.--V"), this);
    statusBar()->addPermanentWidget(labVBatCell);

    labMotorStatus = new QLabel(tr("Disarmed"), this);
    statusBar()->addPermanentWidget(labMotorStatus);
 
    labConnStatus = new QLabel(tr("Disconnected"), this);
    statusBar()->addPermanentWidget(labConnStatus);

    //QTimer *timer = new QTimer(this);
    //connect(timer, SIGNAL(timeout()), SLOT(tick()));
    //timer->start(500);


//    connect( act, &QAction::triggered, mControl, [=]() { mControl->mBox->setCurrentIndex(1); });
//    connect( act, &QAction::triggered, mControl, [=]() { QMessageBox::about(this, "Hello msg", "Hello!"); });
    


//===========================================================
// control dock widget 

    QDockWidget *dock = new QDockWidget( tr("Control Panel"), this);
	dock->setAllowedAreas( Qt::LeftDockWidgetArea | Qt::RightDockWidgetArea);
    dock->setFeatures( QDockWidget::DockWidgetMovable | QDockWidget::DockWidgetFloatable | QDockWidget::DockWidgetVerticalTitleBar);
    //dock->setMinimumWidth( 250);

	mControl = new ControlWidget( dock);
    mControl->linkMainWindow( this);
    mControl->mFormSetup->InitValues( mDoc.cSetup() );

	mControl->setMinimumSize( 280, 400);
    dock->setWidget( mControl);
	addDockWidget( Qt::LeftDockWidgetArea, dock);

    dock->setStyleSheet("QDockWidget:title { background-color: rgb(220, 220, 220);}" );
    //self.dockWidget.setStyleSheet("QDockWidget:title {background-color: none;}")

//actions
    QAction* connAct = new QAction(tr("&Connect"), this);
    ////openAct->setShortcuts(QKeySequence::Open);
    connAct->setStatusTip(tr("Open connection"));
    fileToolBar->addAction(connAct);

    discAct = new QAction(tr("&Disconnect"), this);
    ////openAct->setShortcuts(QKeySequence::Open);
    discAct->setStatusTip(tr("Close connection"));
    fileToolBar->addAction(discAct);
    discAct->setDisabled(true);

    connect( connAct, &QAction::triggered, mControl, [=]() { mControl->mBox->setCurrentWidget(mControl->mFormConnect); } );
    connect( discAct, &QAction::triggered, this, &MainWindow::stop_connection );

     //mControl->mBox->setCurrentWidget(  mControl->mFormConnect );
     // 

    armAct  = new QAction(tr("Arm"), this);
    armAct->setStatusTip(tr("Arm motor"));
    fileToolBar->addAction(armAct);
    armAct->setCheckable(true);
    armAct->setDisabled(true);
    mbackArm = false;

    connect( armAct, &QAction::triggered, this, &MainWindow::arm );

//===========================================================
// output  

    //this->setCentralWidget( splitter);
    mOutput = new TabWidget( &mDoc, this);
    //mOutput->mDataTab->setModel( &mDoc.rData() );
    //mOutput->mGraphTab->reinitData( &mDoc.rData() );

	mOutput->setMinimumSize( 350, 300);
    this->setCentralWidget( mOutput);


    // connect / disconnect
    connect( mControl->mFormConnect->btnConnect, &QPushButton::released, this, &MainWindow::start_connection );
    connect( mControl->mFormConnect->btnDisconnect, &QPushButton::released, this, &MainWindow::stop_connection );

    // serial com
    connect( &mthSerial, &SerialThread::connected, this, &MainWindow::connected);
    connect( &mthSerial, &SerialThread::response, this, &MainWindow::receive);
    connect( &mthSerial, &SerialThread::error, this, &MainWindow::errorHandler);
    connect( &mthSerial, &SerialThread::timeout, this, &MainWindow::timeoutHandler);

    // debug_tab
    connect( mOutput->mDebugTab->btnSend, &QPushButton::released, this, &MainWindow::send );

    // terminal_tab
    connect( mOutput->mTermTab->mpbtnOpenTerm, &QPushButton::released, this, [=]() { this->stopHBeat(); this->send_cmnd( THSP_SHELL_START); } );
    connect( &mthSerial, &SerialThread::start_terminal, this, &MainWindow::start_terminal);
    connect( mOutput->mTermTab, &TerminalView::restoreSerial, this, &MainWindow::stop_terminal );
    //connect( &mthSerial, &SerialThread::start_terminal, this->mOutput->mTermTab, &TerminalView::enableTerminal);
    //connect( mOutput->mTermTab, &TerminalView::restoreSerial, this, [=]() { this->mthSerial.terminalStopped(); } );

    // form setup
    connect( mControl->mFormSetup->btnSave, &QPushButton::released, this, &MainWindow::applySetup );
    
    // form measurement
    connect( mControl->mFormMeasurement->btnMeasureStart, &QPushButton::released, this, [=]() { this->send_cmnd( THSP_DATASTREAM_START); } );
    connect( mControl->mFormMeasurement->btnMeasureStop, &QPushButton::released, this, [=]() { this->send_cmnd( THSP_DATASTREAM_STOP ); } );

    // TODO :: check if motor is armed
    connect( mControl->mFormMeasurement->btnMotorStart, &QPushButton::released, 
             this, [=]() { this->send_cmnd( THSP_MOTOR_SET_COMMAND, mControl->mFormMeasurement->spinMotorOutput->value()); } );
    connect( mControl->mFormMeasurement->btnMotorStop, &QPushButton::released, this, [=]() { this->send_cmnd( THSP_MOTOR_STOP); } );


        //connect( mOutput->mGraphTab, &GraphView::resetMeasurement, &mDoc, &Document::resetMeasurement);

    //connect( this, &MainWindow::dataChanged, this->mOutput, &TabWidget::onDataChenged);
    //connect( this->mOutput->mTermTab->mpConsole, &Console::resetSent, this, &MainWindow::onDeviceReset);


    //connect( mControl->mFormMeasurement->btnMotorStart, &QPushButton::released, this->mAutoControl, &Controller::onStart );
    //connect( this->mControl->mFormAutoMeasure->btnMeasureStart, &QPushButton::released, &this->mAutoControl, &Controller::onStart );
    connect( this->mControl->mFormAutoMeasure->btnMeasureStart, &QPushButton::released, 
            this, [=]() { this->mAutoControl.onStart( &mControl->mFormAutoMeasure->cList() ); } );

    connect( this->mControl->mFormAutoMeasure->btnMeasureStop, &QPushButton::released, 
            &this->mAutoControl, &Controller::onStop );

    connect( this, &MainWindow::dataReceived, &this->mAutoControl, &Controller::onDataReceived );

    connect( this->mControl->mFormProcess->pushButton_Process, &QPushButton::released, this, [=]() { this->onProcess( &mDoc.cData() ); } );
}


MainWindow::~MainWindow()
{
}


void MainWindow::start_terminal()
{
    //QQueue<ThspMessage> queMsg;
    //mthSerial.getReply( queMsg);

    //this->stopHBeat();
    this->mOutput->mTermTab->enableTerminal();
}

void MainWindow::stop_terminal()
{
    this->mthSerial.terminalStopped();
    this->startHBeat();
}



void MainWindow::reset_tool()
{
    stopHBeat();
    this->send_cmnd( THSP_RESET);
//    this->after_disconnect();
}


void MainWindow::onDeviceReset()
{
	qDebug() << "MainWindow ::  'reset' captered !!!";
}

void MainWindow::onProcess( const MeasurementData* data)
{
    int ibeg = 0;
    int iend = (int)data->size();

    mAnalyzer.SetMargins( mControl->mFormProcess->spinBox_Beg->value(), 
                          mControl->mFormProcess->spinBox_End->value() );

    this->mControl->mFormProcess->pushButton_Process->setDisabled(true);

    mAnalyzer.DoAnalyze( mDoc.rResult(), std::make_pair(ibeg, iend), data);
    
    this->mControl->mFormProcess->pushButton_Process->setEnabled(true);
}

void MainWindow::mouseReleaseEvent(QMouseEvent* event)
{
    if (event->button() == Qt::MiddleButton)
    {

        if ( this->isArmed() )
        {
            this->stopMotor();
            this->stopMeasurement();
            //this->arm(false);

            //mAutoControl.onStop();

            //this->stopMotor();
            //this->stopMeasurement();

            //emit stopped();
            QMessageBox::information(this, "info", "Emergency Stop", QMessageBox::Yes);
        }
    }
}


void MainWindow::newFile()
{
    QMessageBox::StandardButton reply;
    reply = QMessageBox::question(this, "New Document", "Are you sure to discard all current data?",
                                QMessageBox::Yes|QMessageBox::No);

    if (reply == QMessageBox::Yes) 
    {
        qDebug() << "Document reset";
        mDoc.Reset();

        mOutput->mDataTab->setModel( &mDoc.rData() );
        mOutput->mGraphTab->reinitData( &mDoc.rData() );
    }
}

void MainWindow::open()
{
    QMessageBox::StandardButton reply;
    reply = QMessageBox::question(this, "Open Document", "Are you sure to discard all current data?",
                                QMessageBox::Yes|QMessageBox::No);

    if (reply == QMessageBox::Yes) 
    {
        //infoLabel->setText(tr("Invoked <b>File|Open</b>"));
        QString fileName = QFileDialog::getOpenFileName(this, tr("Open Document"), 
            "", tr("thrust measurement data (*.th)"));
        qDebug() << "open file " << fileName;

        if (fileName.length() == 0)
            return;

        mDoc.Load( fileName);
    
        //emit dataChanged();
        this->setSetup();     // apply mDoc.mSetup

        mOutput->mDataTab->setModel( &mDoc.rData() );
        mOutput->mGraphTab->reinitData( &mDoc.rData() );
    }
}

void MainWindow::save()
{
    QFileDialog dialog(this);

    QFileInfo fi( mDoc.cFileName() );
    QString dir = dialog.directory().absolutePath() + "/" + fi.baseName();

    QString fileName = QFileDialog::getSaveFileName(this, tr("Save Document as"), 
        dir, tr("thrust measerement (*.th)"));
    qDebug() << "save file as" << fileName;

    if (fileName.length() == 0)
        return;

    mDoc.Save( fileName);
}

void MainWindow::select_export_tmpl()
{
    QString fileName = QFileDialog::getOpenFileName(this, tr("Select report template"), mDoc.cTmplName(), tr("Latex template (*.ttex)"));
    qDebug() << "Select report template" << fileName;

    if (fileName.length() == 0)
        return;

    mDoc.rTmplName() = fileName;
}

void MainWindow::export_rep()
{
    QFileDialog dialog(this);

    QFileInfo fi( mDoc.cFileName() );
    QString dir = dialog.directory().absolutePath() + "/" + fi.baseName();

    QString fileName = dialog.getSaveFileName(this, tr("Export report"), 
        dir, tr("Latex Report (*.tex);;Text Report (*.txt)"));
    qDebug() << "export report file as" << fileName;

    if (fileName.length() == 0)
        return;

    mDoc.GenerateReport( fileName);
}


void MainWindow::settings()
{
    DlgSettings dialog( this);

    dialog.initValues( this->mSetup.cConfig() );
    int res = dialog.exec();
    if ( res == QDialog::Accepted )
    {
        bool bwrite = ! dialog.compareValues( this->mSetup.cConfig() );
        dialog.fetchValues( this->mSetup.rConfig() );


        if ( bwrite )
        {
            // TODO :: send new config and reset tool
            ThspMessage msg;

            this->mSetup.packCfgMotor(msg);
            mthSerial.request( ESerialRequest::TRANSMIT, msg );        

            this->mSetup.packCfgStg(msg);
            mthSerial.request( ESerialRequest::TRANSMIT, msg );        

            this->mSetup.packCfgAdc(msg);
            mthSerial.request( ESerialRequest::TRANSMIT, msg );        

            this->mSetup.packCfgRpm(msg);
            mthSerial.request( ESerialRequest::TRANSMIT, msg );        

            this->mSetup.packCfgConvert(msg);
            mthSerial.request( ESerialRequest::TRANSMIT, msg );

            ////QTimer::singleShot(200, this, &MainWindow::ack_settings);
            //// THSP_WRITE_CONFIG_TO_FLASH

            this->send_cmnd( THSP_WRITE_CONFIG_TO_FLASH);
            this->reset_tool();
            QMessageBox::information( this,	tr("Info"), "Settings has been written to internal flash and the tool has been rebooted" );
        }
    }
}

void MainWindow::about()
{
    QMessageBox msgBox;
    msgBox.setText( tr("The <b>ThrustApp</b> is used for managing the thrust measurement tool.\n") );
    //msgBox.detailedText( tr(GIT_COMMIT_ID) );
    QString str = mDoc.cHeader().strBoardInfo() + "\n" + mDoc.cHeader().strSoftInfo() + "\n" + mDoc.cHeader().strBuildInfo();
    msgBox.setInformativeText( str);
    msgBox.setInformativeText(
        "ThrustApp:\n\tCommit SHA\t" + QString(GIT_COMMIT_ID_SHORT) + "\n\tCommit date\t" + QString(GIT_COMMIT_DATE) + "\n"
        + "Tool Firmware:\n\t" + mDoc.cHeader().strBoardInfo() + "\n\t" + mDoc.cHeader().strSoftInfo() + "\n\t" + mDoc.cHeader().strBuildInfo()
    );
    msgBox.setStandardButtons(QMessageBox::Ok);
    msgBox.setDefaultButton(QMessageBox::Ok);
    int ret = msgBox.exec();

    //QMessageBox::about(this, tr("About Menu"),
    //        tr("The <b>ThrustApp</b> is used for managing the thrust measurement tool.\n")
    //    + mpDoc->strBoardInfo() + "\n"+ mpDoc->strSoftInfo() + "\n"+ mpDoc->strBuildInfo() );
    //msgBox.setInformativeText("Do you want to save your changes?");
}

void MainWindow::setSetup()
{
    const MeasurementSetup& setup = this->mDoc.rSetup();

    mControl->mFormSetup->editMotorName->setText( setup.cMotorName() );
    mControl->mFormSetup->spinMotorKV->setValue( setup.cMotorKV() );
    mControl->mFormSetup->spinMotorPolesCount->setValue( setup.cMotorPoles() );

    mControl->mFormSetup->editPropName->setText( setup.cPropName() );
    mControl->mFormSetup->spinBladeCount->setValue( setup.cPropBlades() );

    mControl->mFormSetup->editComment->setText( setup.cComment() );


    if ( setup.cEscTelemEnabled() ) 
        mControl->mFormSetup->checkBox_EscTelem->setChecked(true);

    //if ( setup.cCurZeroEnabled() )
    //    mControl->mFormSetup->checkBox_CurrZero->setChecked(true);

    // TODO :: set curzero and rpm sources / notify board

    // TODO :: could be disconnected
    //if ( setup.cEscTelemEnabled() || setup.cRpmSource() == ERpmSource::EscTelem )
    //{
    //    mthSerial.request( ESerialRequest::TRANSMIT, ThspMessage( THSP_PACKET_COMMAND, THSP_ESCTELEM_START) );        
    //}
    //else
    //{
    //    mthSerial.request( ESerialRequest::TRANSMIT, ThspMessage( THSP_PACKET_COMMAND, THSP_ESCTELEM_STOP) );        
    //}

}

void MainWindow::applySetup()
{
    // update document setup
    MeasurementSetup& setup = this->mDoc.rSetup();

    setup.rMotorName() = mControl->mFormSetup->editMotorName->text();
    setup.rMotorKV() = mControl->mFormSetup->spinMotorKV->value();
    setup.rMotorPoles() = mControl->mFormSetup->spinMotorPolesCount->value();

    setup.rPropName() = mControl->mFormSetup->editPropName->text();
    setup.rPropBlades() = mControl->mFormSetup->spinBladeCount->value();

    setup.rComment() = mControl->mFormSetup->editComment->text();

    setup.rCurZeroSource() = ECurrZeroSource::None;
    if ( mControl->mFormSetup->radioButton_AutoZ->isChecked() )
        setup.rCurZeroSource() = ECurrZeroSource::Auto;
    else if ( mControl->mFormSetup->radioButton_WithZ->isChecked() )
        setup.rCurZeroSource() = ECurrZeroSource::Sensor;
    else if ( mControl->mFormSetup->radioButton_ManualZ->isChecked() )
        setup.rCurZeroSource() = ECurrZeroSource::Manual;

    setup.rRpmSource() = ERpmSource::None;
    if ( mControl->mFormSetup->radioButton_Sensor->isChecked() )
        setup.rRpmSource() = ERpmSource::IrSensor;
    else if ( mControl->mFormSetup->radioButton_Telem->isChecked() )
        setup.rRpmSource() = ERpmSource::EscTelem;

    setup.rEscTelemEnabled() = mControl->mFormSetup->checkBox_EscTelem->isChecked();
//    setup.rCurZeroEnabled() = mControl->mFormSetup->checkBox_CurrZero->isChecked();


    // TODO :: apply new setup to measurement
    
    if ( setup.cEscTelemEnabled() || setup.cRpmSource() == ERpmSource::EscTelem )
    {
        mthSerial.request( ESerialRequest::TRANSMIT, ThspMessage( THSP_PACKET_COMMAND, THSP_ESCTELEM_START) );        
    }
    else
    {
        mthSerial.request( ESerialRequest::TRANSMIT, ThspMessage( THSP_PACKET_COMMAND, THSP_ESCTELEM_STOP) );        
    }

    //if ( mControl->mFormSetup->radioButton_Sensor->isChecked() )
    //{
    //    mthSerial.request( ESerialRequest::TRANSMIT, ThspMessage( THSP_PACKET_COMMAND, THSP_RPM_START) );        
    //}
    //else
    //{
    //    mthSerial.request( ESerialRequest::TRANSMIT, ThspMessage( THSP_PACKET_COMMAND, THSP_RPM_STOP) );        
    //}

    
    mDoc.initConverter( mSetup);
}


void MainWindow::start_connection()
{
    if ( mSerialStat == ESerialStatus::Closed )
    {
        QString portName    = mControl->mFormConnect->comboPort->currentText();
        //QString rate        = mControl->mFormConnect->comboRate->currentText();
        int baudRate        = mControl->mFormConnect->comboRate->currentData().toInt();

        qDebug() << "MainWindow::start_connection() -- port = " << portName.toUtf8() <<  ", baudrate = " << baudRate;

        mthSerial.startConnection( portName, baudRate, 300 );
        mSerialStat = ESerialStatus::Waiting;
        labConnStatus->setText( tr("Waiting") );
    }
    else
    {
        qDebug() << "MainWindow::start_connection() -- serial is not closed";
    }
}

void MainWindow::stop_connection()
{
    if ( mSerialStat == ESerialStatus::Open )
    {
        qDebug() << "MainWindow::stop_connection() -- closing connection";
        mthSerial.closeConnection();
    }
}

void	MainWindow::connected( bool flag)
{
    if ( flag)
    {
		mControl->mFormConnect->btnConnect->setDisabled( true);

        // gather info
        qDebug() << "MainWindow::connected() -- gathering info";

        mthSerial.request( ESerialRequest::TRANSMIT, ThspMessage( THSP_PACKET_COMMAND, THSP_API_VERSION) );        
        QTimer::singleShot(200, this, &MainWindow::check_connection);
        
        qDebug() << "MainWindow::connected() -- serial is OPEN";

        this->startHBeat();
    }
    else
    {
        after_disconnect();

        qDebug() << "MainWindow::connected() -- serial is CLOSED";
    }
}
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

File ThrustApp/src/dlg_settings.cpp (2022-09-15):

#include <QLayout>

#include "dlg_settings.h"


////////////////////////////////////////////////////////////////////////////////////////////////////
// class FormCfgTool
////////////////////////////////////////////////////////////////////////////////////////////////////
FormCfgTool::FormCfgTool(QWidget* parent) : QWidget(parent)
{
    setupUi(this);

    for (int i = 0; i < size_MotorProtocol; ++i)
        this->comboBox_MotorProt->addItem(QString(names_MotorProtocol[i]), i);

    for (int i = 0; i < size_StGaugeRate; ++i)
        this->comboBox_StGSmpls->addItem(QString(names_StGaugeRate[i]), i);

    for (int i = 0; i < size_StGaugeGain; ++i)
        this->comboBox_StGGain->addItem(QString(names_StGaugeGain[i]), i);

    comboBox_MotorProt->setEditable(false);
    comboBox_StGSmpls->setEditable(false);
    comboBox_StGGain->setEditable(false);

    //connect( spinNSamples, static_cast<void (QSpinBox::*)(int)>(&QSpinBox::valueChanged), this, &FormCalibration::updateTime);
}

void FormCfgTool::initValues(const Config& cfg)
{
    //this->comboBox_MotorProt
    this->spinBox_MotorZero->setValue(cfg.groupMotor.zeroOutput);
    this->spinBox_MotorMin->setValue(cfg.groupMotor.minOutput);
    this->spinBox_MotorMax->setValue(cfg.groupMotor.maxOutput);

    this->spinBox_RpmFreq->setValue(cfg.groupRpm.smplFreq);
    this->spinBox_AdcSmpls->setValue(cfg.groupADC.nADCSamples);


    //this->comboBox_StGSmpls
    //this->comboBox_StGGain

    this->comboBox_MotorProt->setCurrentIndex(cfg.groupMotor.protocol);
    this->comboBox_StGSmpls->setCurrentIndex(cfg.groupStrain.sampleRate);
    this->comboBox_StGGain->setCurrentIndex(cfg.groupStrain.gain);
}

void FormCfgTool::fetchValues(Config& cfg)
{
    //this->comboBox_MotorProt
    cfg.groupMotor.zeroOutput = this->spinBox_MotorZero->value();
    cfg.groupMotor.minOutput = this->spinBox_MotorMin->value();
    cfg.groupMotor.maxOutput = this->spinBox_MotorMax->value();

    cfg.groupRpm.smplFreq = this->spinBox_RpmFreq->value();
    cfg.groupADC.nADCSamples = this->spinBox_AdcSmpls->value();


    //this->comboBox_StGSmpls
    //this->comboBox_StGGain

    cfg.groupMotor.protocol = (EMotorProtocol)this->comboBox_MotorProt->currentIndex();
    cfg.groupStrain.sampleRate = (EHX711Rate)this->comboBox_StGSmpls->currentIndex();
    cfg.groupStrain.gain = (EHX711Gain)this->comboBox_StGGain->currentIndex();
}

bool FormCfgTool::compareValues(const Config& cfg)
{
    if (this->spinBox_MotorZero->value() != cfg.groupMotor.zeroOutput )
        return false;
    else if (this->spinBox_MotorMin->value() != cfg.groupMotor.minOutput )
        return false;
    else if (this->spinBox_MotorMax->value() != cfg.groupMotor.maxOutput)
        return false;
    else if (this->spinBox_RpmFreq->value() != cfg.groupRpm.smplFreq)
        return false;
    else if (this->spinBox_AdcSmpls->value() != cfg.groupADC.nADCSamples)
        return false;
    else if (this->comboBox_MotorProt->currentIndex() != cfg.groupMotor.protocol)
        return false;
    else if (this->comboBox_StGSmpls->currentIndex() != cfg.groupStrain.sampleRate)
        return false;
    else if (this->comboBox_StGGain->currentIndex() != cfg.groupStrain.gain )
        return false;
    else
        return true;

    //if (this->spinBox_MotorZero->value() != cfg.groupMotor.zeroOutput ||
    //    this->spinBox_MotorMin->value() != cfg.groupMotor.minOutput ||
    //    this->spinBox_MotorMax->value() != cfg.groupMotor.maxOutput ||
    //    this->spinBox_RpmFreq->value() != cfg.groupRpm.smplFreq ||
    //    this->spinBox_AdcSmpls->value() != cfg.groupADC.nADCSamples ||
    //    this->comboBox_MotorProt->currentIndex() != cfg.groupMotor.protocol ||
    //    this->comboBox_StGSmpls->currentIndex() != cfg.groupStrain.sampleRate ||
    //    this->comboBox_StGGain->currentIndex() != cfg.groupStrain.gain )
    //{
    //    return false;
    //}

    //return true;
}


////////////////////////////////////////////////////////////////////////////////////////////////////
// class FormCfgConvert
////////////////////////////////////////////////////////////////////////////////////////////////////
FormCfgConvert::FormCfgConvert(QWidget *parent) : QWidget(parent)
{
    setupUi(this);

    //connect( spinNSamples, static_cast<void (QSpinBox::*)(int)>(&QSpinBox::valueChanged), this, &FormCalibration::updateTime);
}
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

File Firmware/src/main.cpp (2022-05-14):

/*
 ChibiOS - Copyright (C) 2006..2018 Giovanni Di Sirio

 Licensed under the Apache License, Version 2.0 (the "License");
 you may not use this file except in compliance with the License.
 You may obtain a copy of the License at

 http://www.apache.org/licenses/LICENSE-2.0

 Unless required by applicable law or agreed to in writing, software
 distributed under the License is distributed on an "AS IS" BASIS,
 WITHOUT WARRANTIES OR CONDITIONS OF ANY KIND, either express or implied.
 See the License for the specific language governing permissions and
 limitations under the License.
 */

#include <cmath>
#include <utility>

#include "system/sysdecl.hpp"
#include "util/waitmicro.hpp"

#include "io/io.hpp"
#include "master.hpp"

#include "cli.hpp"

#include "lcd/display_ssd1306.hpp"

#include "driver/motor.hpp"
#include "driver/adc.hpp"
#include "driver/hx711.hpp"
#include "driver/rpm_icu.hpp"

#include "th_measure.hpp"
#include "th_serial.hpp"
#include "th_esctelem.hpp"


#define WITH_LCD_DISPLAY


using blink_def = std::pair<systime_t,systime_t>;

blink_def blink_arr[] = { {250,250}, {125,300}, {80,80} };
uint8_t blink_mode = 1;

//===========================================================================
// Red LED blinker thread, times are in milliseconds.
//===========================================================================
class BlinkerThread: public chibi::BaseStaticThread<128>
{
public:
	BlinkerThread( void)
			: chibi::BaseStaticThread<128>()
	{
	}

protected:
	void main( void) override
	{
		setName( "Blinker");

//		blink_def time(250,150);
//		systime_t time = 250;

		while ( true)
		{
			palClearLine( LINE_LED_BLUE);
			sleep( TIME_MS2I( blink_arr[blink_mode].first));
			palSetLine( LINE_LED_BLUE);
			sleep( TIME_MS2I( blink_arr[blink_mode].second));

//			palToggleLine( LINE_LCD_SPI_CS );
//			palToggleLine( LINE_LCD_SPI_DC );
//			palToggleLine( LINE_LCD_RESET );
		}
	}

};


//===========================================================================
// Heart-beat thread, times are in milliseconds.
//===========================================================================
class HBeatThread: public chibi::BaseStaticThread<128>
{
public:
	HBeatThread( void)
			: chibi::BaseStaticThread<128>(), mpMaster(nullptr)
	{
	}

	void	SetMaster( Master* pmst)	{ mpMaster = pmst; }

protected:
	void main( void) override
	{
		setName( "HBeat");

		while ( true)
		{
			if ( mpMaster)
			{			
				mpMaster->pData()->mux.lock();
				bool bHBeat = mpMaster->pData()->bConnAlive;
				mpMaster->pData()->mux.unlock();

				
				if ( bHBeat )
				{
					palSetLine( LINE_LED_GREEN);
				}
				else
				{
					mpMaster->SetSerialMode( ESerialMode::Command );
					mpMaster->MotorStop();
					mpMaster->MotorDisarm();
					palClearLine( LINE_LED_GREEN);
				}
				
				mpMaster->pData()->mux.lock();
				mpMaster->pData()->bConnAlive = false;
				mpMaster->pData()->mux.unlock();
			}
			
			chibi::BaseThread::sleep( TIME_MS2I( 1300));
		}
	}
	
private:
	Master*			mpMaster;
};



IoMaster	io( (BaseAsynchronousChannel*)&SD_OUTPUT, (BaseAsynchronousChannel*)&SD_SERIAL );
Master		master;

#ifdef WITH_LCD_DISPLAY
DisplayIf	lcd_if( &LCD_IF);
Display		lcd( &lcd_if);	// TODO : add lcd_mutex
#endif

//RpmDev			dev_rpm( &master.pConfig()->groupRpm );


//===========================================================================
static BlinkerThread 	blinker_th;
static HBeatThread		hbeat_th;



systime_t now = 0;

//===========================================================================
// Application entry point.
//===========================================================================
int main( void)
{
	halInit();
	chibi::System::init();


	gpioInit();

	InitSystem();
	shellInit();
	gptInitTimer();

	master.Init();
	io.Start();

	palClearLine( LINE_LED_YELLOW);
	palClearLine( LINE_LED_GREEN);
	palClearLine( LINE_LED_BLUE);



#ifdef WITH_LCD_DISPLAY
	////////////////////////////////////////////////////////
	// LCD init

	lcd_if.Start();
	lcd.Init();

	chibi::BaseThread::sleep( TIME_MS2I( 200));

	lcd.Fill(Black);
	lcd.SetCursor(5, 10);
	lcd.WriteString("Hello !!!", font7x10, White);
	lcd.UpdateScreen();
	chibi::BaseThread::sleep( TIME_MS2I( 800));

	lcd.Fill(Black);
	for ( uint32_t delta = 0; delta < 5; ++delta)
		lcd.Rectangle( 1 + (5*delta), 1 + (5*delta), SSD1306_WIDTH-1 - (5*delta), SSD1306_HEIGHT-1 - (5*delta), White);
	lcd.UpdateScreen();
	chibi::BaseThread::sleep( TIME_MS2I( 500));

	lcd.Fill(White);
	lcd.UpdateScreen();
	chibi::BaseThread::sleep( TIME_MS2I( 500));
	lcd.Fill(Black);
	lcd.UpdateScreen();
	////////////////////////////////////////////////////////
#endif

	master.Start();

	blinker_th.start( NORMALPRIO + 5);
	
	hbeat_th.SetMaster( &master );
	hbeat_th.start( NORMALPRIO );

//	dev_rpm.Init( &RPM_ICUD, RPM_ICU_CH);
//	dev_rpm.Start();

	chibi::BaseThread::sleep( TIME_MS2I( 50));

	while ( true)
	{
		now = chVTGetSystemTime();
		dbg_printf("systime = %d\n", now);

		dbg_puts("HELLO\n" );

//		palToggleLine( LINE_LED_BLUE );
//		palToggleLine( LINE_DEBUG_1 );
//		palToggleLine( LINE_DEBUG_2 );
//		spiSend( &SPID3, 6, "abcdef");

//		if ( palReadLine(LINE_BUTTON) == PAL_LOW)
//		{
//				motor.SetOutput( 1200);
//			 shellStart( (BaseSequentialStream*)&SD_OUTPUT);
//		}

		palToggleLine( LINE_DEBUG_1 );

#ifdef WITH_LCD_DISPLAY
		master.pData()->PrintOnScreen(&lcd);
#endif

//		palToggleLine( LINE_DEBUG_1 );

		chibi::BaseThread::sleep( TIME_MS2I( 50));
	}

	return 0;
}

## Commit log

2022-04-16 initial import
    [thrust_v2-B_Cu.gbl, thrust_v2-B_Mask.gbs, thrust_v2-B_Paste.gbp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]
2022-04-16 stl files for 3dprint added
    [th3 adapter.stl, th3 axle mount.stl, th3 board mount.stl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]
2022-04-16 step files added
    [th3 adapter.stl, th3 axle mount.step, th3 board mount.step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]
2022-04-18 board pics added
2022-04-19 fix curr_zero connection
    [thrust_v2-B_Cu.gbl, thrust_v2-B_Mask.gbs, thrust_v2-B_Paste.gbp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]
2022-04-19 bugfix for incorrect curr_zero_pin
    [adc.cpp, config.hpp, config_def.cpp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]
2022-04-19 board schematic updated
    [thrust_v2.sch]
2022-04-24 settings tested; can be written to the flash using thrustapp
2022-04-25 bugfix for cell volt. in status bar
    [mainwindow.cpp]
2022-05-01 bugfix for cfg. vbat correction; mn2206 + 3 blade prop. measurement added
    [data.cpp, dlg_settings.cpp, mainwindow.cpp]
2022-05-09 mt2212 with prop 10x4.5 added
2022-05-14 .th files converted to current version
2022-09-11 fw TODO: sensor settings added
2022-09-12 fw: stg gain fix
    [config_def.cpp]
2022-09-15 wip: minor fixes; fw defaults for cfg changed
    [config_def.cpp, data.cpp, dlg_settings.cpp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]
2023-04-13 current calibration revisited
    [calib-3kg.xlsx, calib-th3kg_tq2kg.xlsx, current_cal.xlsx]
